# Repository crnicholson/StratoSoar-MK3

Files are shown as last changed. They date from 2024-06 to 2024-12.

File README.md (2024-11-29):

# StratoSoar MK3 - UAVs For the Masses

<!-- **TL;DR**: The StratoSoar project is a low-cost, lightweight UAV designed to be dropped from a weather balloon  at any altitude, aiming for autonomous, efficient flight to selected GPS coordinates. The hope is to get a UAV platform in the hands of educators, researchers, and hobbyists alike since StratoSoar is much smaller, lighter, and cheaper than conventional UAVs.  -->

**TL:DR**: The StratoSoar project is a low-cost, lightweight Unmanned Aerial Vehicle (UAV) designed for deployment from a weather balloon at various altitudes, aiming for autonomous and efficient flight to designated GPS coordinates. By offering a more affordable, compact, and lightweight alternative to conventional UAVs, StratoSoar aims to empower educators, researchers, and hobbyists with an accessible platform for exploration and experimentation. 

## Watch The Video

<!-- **WORK IN PROGRESS** - This project is still in the works. I don't recommend using it yet because it has the potential of being dangerous.

**NEW** - Writing code and making the PCB. 

**STATE as of 7/1/24** - Just starting development! -->

<!-- <div style="max-width: 500px; margin: 0 auto;">
  <div style="position: relative; padding-bottom: 56.25%; height: 0; overflow: hidden; max-width: 100%; height: auto;">
    <iframe style="position: absolute; top: 0; left: 0; width: 100%; height: 100%;" src="https://www.youtube.com/embed/TiqkcGWG4g8" title="StratoSoar MK2/3: A Review" frameborder="0" allow="accelerometer; autoplay; clipboard-write; encrypted-media; gyroscope; picture-in-picture; web-share" referrerpolicy="strict-origin-when-cross-origin" allowfullscreen></iframe>
  </div>
</div>

<br /> -->

YouTube Video (https://www.youtube.com/watch?v=TiqkcGWG4g8&t=1s)

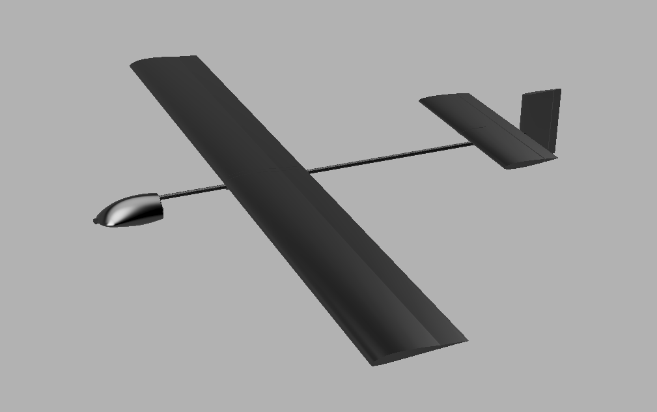
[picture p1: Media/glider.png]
Glider
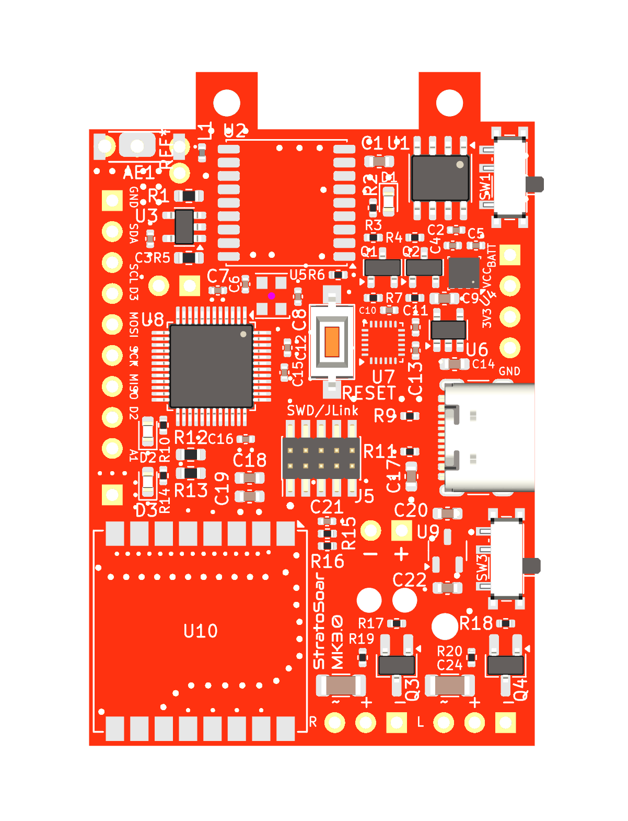
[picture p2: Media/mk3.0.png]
PCB
 | 
-- | --
<i>StratoSoar glider.</i> | <i>StratoSoar MK3.0 circuit board.</i>
Glider | PCB
<i>Computational fluid dynamic sims.</i> | <i>Soldering of the board.</i>

## What Is the StratoSoar Project?

StratoSoar is a low-power, adaptive UAV that is dropped from a weather balloon at approximately 5,000 feet, with plans to reach even higher altitudes soon. The main goal of StratoSoar is to fly to selected GPS coordinates efficiently or choose a closer, more realistic landing site without human interaction. The current aim for StratoSoar is to operate on a single 600 mAh 15 gram LiPo battery for a 10+ hour flight. 

## Now, What Is a UAV?

UAVs, or Unmanned Aerial Vehicles, are autonomous aircraft, usually in the form of planes or drones. They have many applications, such as [delivering medicine, food, and supplies](https://www.flyzipline.com/) to remote areas, participating in aerial combat with the military, and conducting aerial imaging.

### Common Types of UAVs Include:

- Quadcopter (typical drones)
- Fixed-wing aircraft (like StratoSoar)

## StratoSoar vs. Conventional UAVs

### Traditional UAVs Are Typically:

- Large (5-15 meter wingspan)
- Heavy (2-20 kg)
- Expensive ($10,000-10,000,000 USD)
- Closed source and proprietary

### StratoSoar Aims to Overcome These Limitations With:

- Weight: less than 250 grams
- Wingspan: 80 cm
- Cost: less than $150 USD
- Open source and accessible

## What Are the Uses of StratoSoar?

I'm currently considering two main concepts: an educational kit for students and hobbyists or a platform designed to study the aerodynamics of the stratosphere, a field with limited existing resources. Additionally, I'm exploring other ideas such as reusable radiosondes, systems for remote delivery of medicine and parcels, and advanced atmospheric monitoring solutions.

<!-- ## What Includes the StratoSoar Project? What Are the Different Parts of it?

StratoSoar has many different parts, and they all combine to make this project. 

- **Code** - All of the code directory, and the programs needed to run it. These include the main `.ino`s and the accompanying `.cpp` and `.h` files, along with the test files for the IMU and GPS.
- **PCB** - The circuit board is the basis of this project, it interfaces the code with the glider. StratoSoar includes the circuit board files and the schematics and everything needed to build a PCB.
- **3D Files** - StratoSoar requires some 3D printed parts to function, but these files also serve as an interactive build guide. StratoSoar includes the 3D files needed to print parts for the glider and the 3D files to assemble the glider.
- **Media** - The images and such of StratoSoar. 
- **Cutdown Mechanism** - This is the thing that helps you release the glider from the balloon payload - or whatever you want to drop it from. This includes all of the above things but will be in a separate GitHub repository.  -->

## How Does StratoSoar Work at a High Level?

<!-- StratoSoar is attached to a weather balloon via the cutdown mechanism. Once the balloon reaches the desired altitude, the cutdown mechanism drops the glider. The glider then descends, steering its way to specified coordinates. 

StratoSoar takes pride in being highly configurable and hackable, so there are many ways you change how it comes down built into the code. 

StratoSoar uses data from an IMU that goes through a Kalman filter to receive accurate AHRS, or Attitude Heading Reference System. This can tell StratoSoar the pitch, yaw, and roll of the glider. Then, StratoSoar integrates a GPS module to get the GPS coordinates. Both the GPS and the AHRS are used to compute the azimuth to find the turning angle of the glider. The turning angle tells the glider how much it needs to turn to be facing the correct yaw that will get the glider to the target location. Additionally, an algorithm is used to get the distance between the glider location's and the target location. 

With the turning angle computed, a PID mechanism is used to control the servo attached to the rudder of the glider. This PID mechanism learn from it's mistakes and can accurately aim the glider in the correct direction. 

Additionally, the glider beacons it's location at a configurable interval with LoRa for tracking. It also allows for a camera module to be added on to take photos and video. 

The glider will fly to the selected coordinates, and depending on the user configuration, will either spiral down or release a parachute above the coordinates once it has reached them to safely descend. Additionally, if the glider is too low in altitude, prior to the flight the user can enter closer coordinates as backup landing locations.  -->

StratoSoar MK3 is an advanced autonomous glider designed to operate at high altitudes, such as those reached by weather balloons. The glider is attached to a weather balloon via a cutdown mechanism. Once the balloon reaches the desired altitude, the cutdown mechanism releases the glider, initiating its descent. The glider then navigates autonomously to specified coordinates, using a combination of sensors, advanced algorithms, and low-power electronics.

### Core Components and Functionality:

- **Autopilot System**:
    - **GPS and IMU Integration**: StratoSoar uses a custom GPS module and an IMU, both designed for low-power operation. The IMU data is processed through a Kalman filter to provide accurate Attitude Heading Reference System (AHRS) data, including pitch, yaw, and roll. This information, combined with GPS coordinates, enables precise navigation.
    - **Advanced Waypoint Navigation**: The waypoint navigation system is designed for complex flight paths, incorporating advanced turning algorithms to ensure smooth and accurate direction changes.
    - **Servo Control with PID**: A PID control mechanism governs the rudder’s servo, ensuring precise adjustments to the glider's course based on real-time feedback.

- **Communication and Data Logging**:
    - **LoRa Telemetry**: The glider continuously beacons its location via LoRa communication, which includes forward error correction for reliable data transmission. This allows for real-time tracking and data collection.
    - **Data Logging**: Critical flight data, including sensor readings and GPS coordinates, are logged using a combination of SD card and EEPROM storage, optimized for low power consumption.
    - **Camera**: If configured, the glider uses a custom designed camera module to take photos at specific coordinates or record the entire flight.  

- **Modularity and Customization**:
    - **Hackability**: StratoSoar is designed to be highly configurable and hackable. Users can customize its descent strategy, whether by spiral descent, parachute deployment, or alternative landing locations. The codebase is modular, allowing for easy modifications or the addition of new features.
    - **Camera Module**: An optional low-power camera module can be added to capture photos or video during the flight, with Python scripts available for post-processing the footage.

- **Ground Station and Data Handling**:
    - **Ground Station**: The ground station, built on an ESP32 platform, receives telemetry data from the glider via LoRa. It logs this data locally and communicates with a server using HTTP requests. A Flask-based uploader script then transfers the data to SondeHub for analysis and storage.

- **PCB Design**:
    - **StratoSoar MK3 PCB**: The main PCB, optimized for power efficiency, size, and cost, integrates over 100 components, managing the various systems onboard.
    - **Additional PCBs**: Supporting PCBs, such as those for the GPS module, LoRa communication, camera, and IMU, are designed for specific tasks, enhancing the glider's overall functionality.

### Operation and Recovery:

Upon release from the weather balloon, StratoSoar begins its guided descent following waypoints or single target coordinate. It calculates the optimal flight path using its GPS and AHRS data, making real-time adjustments to its trajectory through the PID-controlled servo system. Depending on user configurations, the glider can either glide smoothly to the target coordinates, initiate a spiral descent, or deploy a parachute for a safe landing.

If the glider's altitude drops below a certain threshold, backup landing coordinates can be used to ensure a safe recovery. Throughout the flight, the glider’s location is continuously transmitted, allowing for easy tracking and recovery.

## File System and More Project Info

I'm only listing the key items, leaving out all the unnecessary stuff. This should give you a general sense of the project and all its features. Note that this is also only stuff I did during Hack Club Arcade.

- `Code/autopilot`: (5000 lines of code!)
    - `autopilot.ino`: The script that ties all of these files together.
    - `gps.cpp`: GPS code custom-made for low-power.
    - `waypoint.cpp`: Custom waypoint flight with advanced turning.
    - `lora.cpp`: LoRa communications with complex forward error correction.
    - `sd.cpp` + `eeprom.cpp`: Data logging in a low-power manner.
    - `servo.cpp`: Ultra low-power servo functions.
    - `bme280.cpp`: Weather data sensor.
    - `imu.cpp`: An interial measurement unit running a Kalman filter.
- `Code/groundStation`: 
    - `groundStation.ino`: The code for the receiving station of the LoRa telemetry, uses ESP32 and HTTP requests to communicate with the server, also locally logs data. 
    - `uploader/flaskUploader.py`: A Flask server that uses an API to put all the data on SondeHub. 
- `Code/camera`: Utilization of a low-power camera module and Python scripts for conversion.
- `Code/calculator`: Python script to parametrically create flying wing glider. 
- `PCB/StratoSoar-MK3.0`: The main PCB consisting of over 100 components, optimized for power, size, and cost.
- `PCB/gpsBreakout`: A PCB designed for testing a cheap, $2 Chinese GPS module.
- `PCB/loRa`: The ground station to receive the glider's data. 
- `PCB/camera`: A breakout board for a low-power camera module. 
- `PCB/imuBreakout`: One of the first breakout boards made for a new Interial Measurement Unit. 
- `3D Files/cardboardGlider`: Parametric Fusion 360 design for a folding origami glider. 
- `3D Files/StratoSoar Rev2 v36`: High efficiency glider.

## A Quick Note on MK1, MK2, Naming, and Revisions

StratoSoar MK1 was the precursor and the spark to StratoSoar MK2. StratoSoar MK1 was officially developed from October 1st to July 30th, although StratoSoar MK2 was unofficially being worked on in the months of March through June. StratoSoar MK1 failed to fly autonomously, and it also failed to release from the balloon. Major upgrades have been made since then.

StratoSoar MK2 officially started on October 1st, and will end has now ended. It was a success. 

StratoSoar MK3 officially started on June 1st, and will end in quite some time when I launch it from a weather balloon. A new major revision (eg. MK4) will come out every time when I release the glider from the balloon in the Summer. After the Summer, work on the next revision begins, with many updates and new features. 

<!-- A new sub-revision (for lack of better word) comes out every time I make a new PCB. For example, my first version of my PCB was MK2.0. At the time of writing, the current version of StratoSoar is MK2.1. A new version of 3D model is denoted by the Rev number. Rev starts at 0. 0 and 1 are not shown in this repo because they didn't turn out very good. The physical gliders are denoted by the 3D model number. Sometimes a small change is made with glider so the name of the glider is Rev x.x, for example. Sometimes the same happens with the 3D model, again it would be x.x. To put this in practice, the final glider may be MK2.5 Rev 7.3.1. The code has no version history in the way the 3D models and the PCB do. -->

Also, I use "we" a lot in this writing. This usually refers to myself or this project, but it also refers to my small team over at New England Weather Balloon Society.

One last thing. When I refer to StratoSoar, I am referring to the project as a whole, but more specifically, the most recent version. 

<!-- ## Watch my Talk About StratoSoar MK2 The North East HamXpo! -->

## Is This Legal?
Yes! During flight, the ground operator has no ***direct*** control over the flight path, i.e. via a radio. Because of this, and it being unpowered, it qualifies as a free flight glider. Free flight gliders have very little regulations. You can think of them as a paper airplane. 

## Can I Buy a Kit or a Complete Product?

Currently, StratoSoar is not available to purchase online as a kit or complete product. We have plans in the next few years to release a kit for schools, education centers, hobbyists and a complete product for industry at an affordable price. You are welcome to make one in the mean time!

## How Can I Make One? Are There Docs?

One of the goals of StratoSoar was to make an affordable and open source system for anyone to perform stratospheric research, so all the files are available for free. This means that you can construct StratoSoar from scratch. **A guide to do this will be available soon.**

<!-- It is still in the works, but you can check out `DOCS.md` under the `Docs` folder.**  -->

## Helpful Sources and Credits

I'm in the midst of compiling this.

## Cutdown Mechanism

[See my other WIP GitHub repo.](https://github.com/crnicholson/Cutdown-Mechanism)

## Funding and Support

We currently have <u>**very**</u> limited funding to complete this project. We would **love any donations or sponsorships** we could get to elevate (no pun intended) this project to the next level. If you don't want to donate, but want to help out, we would love your support with other areas of this project. Reach out to me if you have interest at:

- [newbsballoons@gmail.com](mailto:newbsballoons@gmail.com) (organization email, recommended).

- [charlienicholsonr@gmail.com](mailto:charlienicholsonr@gmail.com) (personal email).

## Special Thanks

This project would not be possible without the following individuals:

- Max Kendall (W0MXX) for working closely together with me.

- Mike Malis for helping with the design of the glider. 

- Brett Miwa for schematic review, PCB design, electrical theory, and boost converter circuitry design.

- Bob Phinney (K5TEC) for providing NEST and securing funding.

- Mark Jessop (VK5QI) for answering all of my questions.

- Mike Hojnowski (KD2EAT) for PCB design and hardware/software debugging.

- Paul Hamilton for helping me with FAA regulations.

- My parents!

And these entities:

- Hack Club, for providing support for projects like this. 

- New England Sci-Tech (NEST) for providing a maker space to work, funding, and hosting NEWBS.

- New England Weather Balloon Society (NEWBS) for expertise and the opportunity.

- Bagel Fund, for providing funding. 

## Affiliate Programs and Projects

- **Hack Club** - Hack Club is a non-profit designed for teenagers that provides support for projects like this. 
- **NEWBS** - Max and Seth Kendall of NEWBS, or New England Weather Balloon Society, are helping me launch my project from a balloon. They are dedicated to helping people in New England launch weather balloons. 
- **New England Sci-Tech** - Bob Phinney of NEST is hosting NEWBS. NEST is a great maker space. If you are in the Greater Boston Area, go check them out!
- **StratoScience** - This is the official class that I'm in helping me launch my project. This is a high altitude engineering class for teens. Check them out if your are in the Greater Boston area!

## Still Have Questions?

Do you have any questions? Are the docs incomplete and you want to ask anything? Do you just want to say hi (or how cool my project is!)?

Reach out to me at [charlienicholsonr@gmail.com](mailto:charlienicholsonr@gmail.com).

## Flights

# Mid August

The glider was realeased from 5,000 feet. You can see the launch video [here](https://www.youtube.com/watch?v=DZU_8TDUlJg). You can find data on the release [here](https://www.youtube.com/watch?v=TiqkcGWG4g8).

## License

Both the software and documentation are under the [GNU GPL v3 license](https://choosealicense.com/licenses/gpl-3.0/). The hardware and the 3D files are under the [CERN Open Hardware Licence Version 2 - Strongly Reciprocal](https://choosealicense.com/licenses/cern-ohl-s-2.0/). The media is under the [CC BY 4.0 DEED](https://creativecommons.org/licenses/by/4.0/).

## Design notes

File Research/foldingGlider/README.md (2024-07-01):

# This is for Hack Club Arcade

This is a glider that is very easy to manufacture. You simply cut it out with a laser, plotter, CNC, or another tool and fold it up. It is designed to be outfitted with my custom electronics and to be used in disaster releif. My goal is for the entire bundle to be less than $75 to make it open to everyone. 

# Gallery

All images should be in the sessions on Hack Club Slack.

# Research Sessions

### [Session](https://hackclub.slack.com/archives/C06SBHMQU8G/p1719795937090849)

During this session, I delved into researching flying wing design. I started by watching videos and reading documents, focusing on aspect ratios and design parameters like taper, sweep, wingspan, chord, area, and wing cube loading (WCL). I decided on an aspect ratio of 6 for my model and aimed for a WCL of 7. I encountered some challenges with a Python script I was developing but managed to fix it to calculate surface area correctly based on weight and WCL. By the end of the session, I was working on calculating the wing sweep angle.

### [Session](https://hackclub.slack.com/archives/C06SBHMQU8G/p1719789537091729)

Swept wings decrease drag but also reduce lift and are beneficial near supersonic speeds. They act like a lever, helping balance the center of gravity (CG) and provide better leverage for the plane’s elevons.

However, swept wings can cause yaw and roll cycles due to uneven lift, leading to instability. Wing fences and tip fins improve stability by mitigating turbulence and must be positioned behind the CG to maintain positive stability. Tip fins also enhance yaw stability by preventing air from below the plane from causing additional drag.

The videos explain the concepts of center of gravity (CG) and center of pressure (CP). CG is fixed, but CP changes with the angle of attack, which can cause instability. On conventional aircraft, tails provide a downward force to balance CG and CP. It’s crucial to place the CG far in front of the CP for stability, similar to a dart’s design.

Reflex, the upturned trailing edge, acts like a tail for stability but decreases efficiency. Symmetrical airfoils are used for better stability and to reduce the need for reflex.

### [Session](https://hackclub.slack.com/archives/C06SBHMQU8G/p1719598218516089)

So to summarize my last session, you can cut foam board with a 5 watt laser diode only if the foam board is black because of the wavelengths interfering. Black foam board is about 4.50 per sheet, so not too expensive. I may go this route.

I watched this video: https://www.youtube.com/watch?v=T5YABSqPOY0. It was very helpful for me to understand cutting cardbaord on a laser diode. It seems to work much better than a high power CO2 laser, like a Glowforge. It does take some time, though. The person had the speed at 30 mm/s and 40 PASSES, which is a lot of passes. If I get a laser, I may experiment with fewer passes and decreased speed to do it quicker. This seems like the best solution for manufacturing cardboard sheets, seeing as diode lasers are much larger than CO2 lasers for much cheaper. I might buy one, we’ll see.

So I took a break to research laser cutter safety. They aren’t very safe and there’s no way my parents are letting me get one even if I pay for it. This is sad because they are perfect for my needs. However, my maker space has one but the working space of it is very limiting. Because of this I will research alternate routes.

More research to report! There aren’t any machines that can cut cardboard as well as a laser. However, a Cricut can cut cardboard quite well. The only problem with the Cricut is that they have a maximum width of 12 inches. That isn’t enough. I shall continue researching until I find a way to cut this cardboard. I may look into that needle cutter again because of how cheap and easy to use it is. It is also safe to use which is nice. (edited) 

I watched this video, it wasn’t very helpful: https://www.youtube.com/watch?v=N42lrWzGQjw. I also watched this video: https://www.youtube.com/watch?v=kho1yvjRKxQ, and it shows how CNCs can cut cardboard quite well. Unfortunately, CNCs are big and expensive and I don’t have one and neither does my maker space. I guess I need to build one! (edited) 

Did more research and I found out that I cannot cut foam core with my hot wire CNC cutter. I think the only option left now is to adapt my CNC foam cutter to use a needle cutter or a drag cutter. I will research both.

So, yes it is possible to make a CNC drag cutter. This seems really cool. The thing I’m wary about though is if my CNC foam cutter can hold all the heavy stuff to control the drag cutter.

### [Session](https://hackclub.slack.com/archives/C06SBHMQU8G/p1719593377357869)

I plan to research laser cutters, specifically for cutting foam and cardboard. Initially, it seems that a diode laser might be suitable for cutting foam board, but there are other considerations. For instance, some people suggest using a CO2 laser, which is much more expensive, around $3,000, compared to diode lasers, which cost around $200.

According to Reddit, the type of foam board matters significantly. They recommend using foam board with a cardboard backing, known as art board. Additionally, it's crucial to have an air assist feature to blow away flames that may arise during cutting, as some foam materials are prone to catching fire. Good ventilation or wearing a respirator is also essential for safety.

White foam doesn't work well with lasers because it reflects all colors. For such materials, a special foam cutter or a CO2 laser is required. I came across a discussion about a needle cutter on the LightBurn Software forum. The needle cutter operates by moving a needle up and down rapidly, penetrating the foam board to make precise cuts. However, constructing a needle cutter seems quite labor-intensive.

Given these insights, it's clear that diode lasers are not suitable for cutting certain types of foam due to their different wavelengths.

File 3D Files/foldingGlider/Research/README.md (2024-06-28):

# This is for Hack Club Arcade

This is a glider that is very easy to manufacture. You simply cut it out with a laser, plotter, CNC, or another tool and fold it up. It is designed to be outfitted with my custom electronics and to be used in disaster releif. My goal is for the entire bundle to be less than $75 to make it open to everyone. 

# Gallery

All images should be in the sessions on Hack Club Slack.

# Research Sessions

## https://hackclub.slack.com/archives/C06SBHMQU8G/p1719598218516089

So to summarize my last session, you can cut foam board with a 5 watt laser diode only if the foam board is black because of the wavelengths interfering. Black foam board is about 4.50 per sheet, so not too expensive. I may go this route.

I watched this video: https://www.youtube.com/watch?v=T5YABSqPOY0. It was very helpful for me to understand cutting cardbaord on a laser diode. It seems to work much better than a high power CO2 laser, like a Glowforge. It does take some time, though. The person had the speed at 30 mm/s and 40 PASSES, which is a lot of passes. If I get a laser, I may experiment with fewer passes and decreased speed to do it quicker. This seems like the best solution for manufacturing cardboard sheets, seeing as diode lasers are much larger than CO2 lasers for much cheaper. I might buy one, we’ll see.

So I took a break to research laser cutter safety. They aren’t very safe and there’s no way my parents are letting me get one even if I pay for it. This is sad because they are perfect for my needs. However, my maker space has one but the working space of it is very limiting. Because of this I will research alternate routes.

More research to report! There aren’t any machines that can cut cardboard as well as a laser. However, a Cricut can cut cardboard quite well. The only problem with the Cricut is that they have a maximum width of 12 inches. That isn’t enough. I shall continue researching until I find a way to cut this cardboard. I may look into that needle cutter again because of how cheap and easy to use it is. It is also safe to use which is nice. (edited) 

I watched this video, it wasn’t very helpful: https://www.youtube.com/watch?v=N42lrWzGQjw. I also watched this video: https://www.youtube.com/watch?v=kho1yvjRKxQ, and it shows how CNCs can cut cardboard quite well. Unfortunately, CNCs are big and expensive and I don’t have one and neither does my maker space. I guess I need to build one! (edited) 

Did more research and I found out that I cannot cut foam core with my hot wire CNC cutter. I think the only option left now is to adapt my CNC foam cutter to use a needle cutter or a drag cutter. I will research both.

So, yes it is possible to make a CNC drag cutter. This seems really cool. The thing I’m wary about though is if my CNC foam cutter can hold all the heavy stuff to control the drag cutter.

## https://hackclub.slack.com/archives/C06SBHMQU8G/p1719593377357869

Note: being lazy with the spelling, sorry! :)

will research lasercutters

i need to laser cut foam and cardboard

i also need to research flying wings bc I have no clue about their aerodynamics

i’ll document my findings in a readme file

seems like a diode laser is the best for cutting foam board

okay, some people are saying co2 laser

co2 lasers are like 3,00 dolla though

and diode lasers are only $200

reddit also says that the foam board matters

they say to get the foam board that has a cardboard backing - called art oard

and you need air assist to blow away the flames if they show up - some foam makes flames

they also recommend having good ventilation or wearing a respirator

oh, interesting

white foam doesn’t work very well because it reflects all color

you apparently need a special foam cutter or a co2 laser

i shall research this needle cutter

https://forum.lightburnsoftware.com/t/cutting-dollar-tree-foam-board/97158

so the needle cutter is similar to blot which is pretty rad

just a bit bigger

so it works by having a needle go up and down really really quickly

it basically penetrates the foam board and makes a fairly precise cut

it seems like it would be too much work to make though

so I’m going to research further into lasers

okay, diode lasers can’t do it! interesting! it’s mainly bc of the different wavelength

you need a co2 laser

which are super expensive.

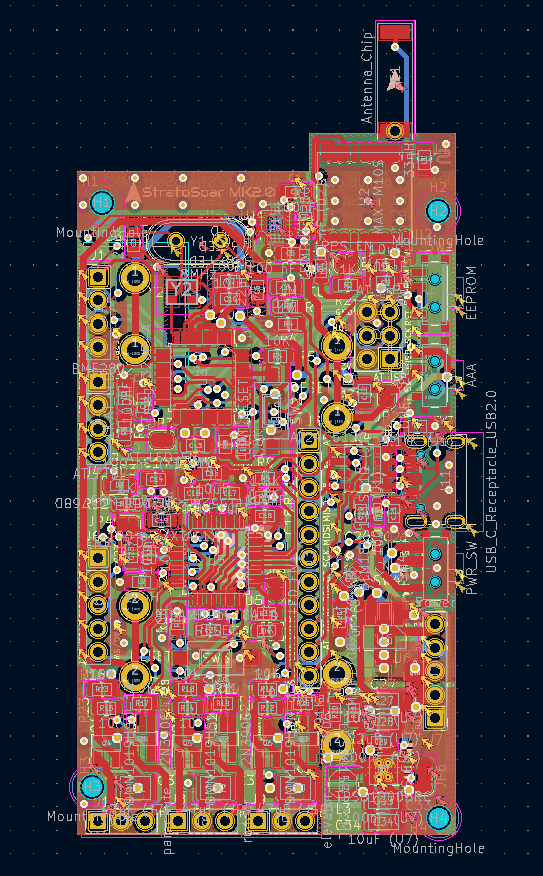
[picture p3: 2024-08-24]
Media/video/Electronics/MK2.0 board design.png

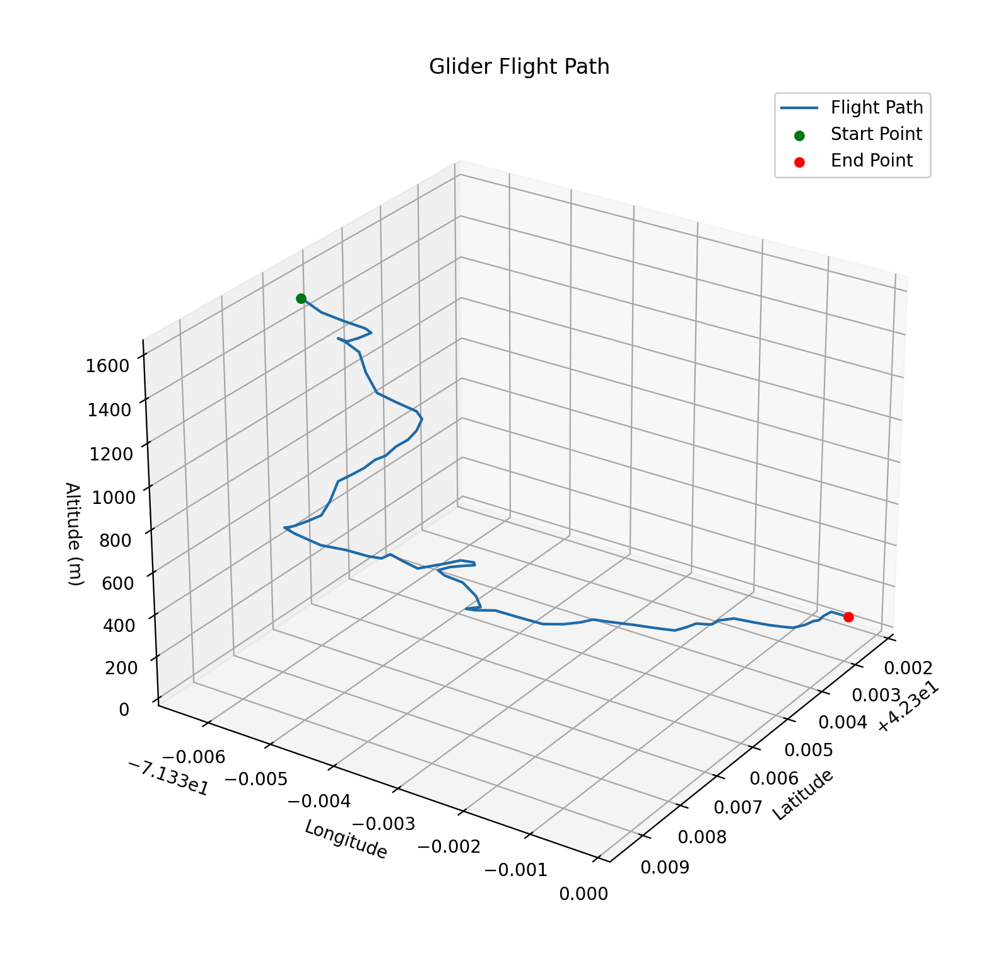
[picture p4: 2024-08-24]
Media/video/Flight path.png

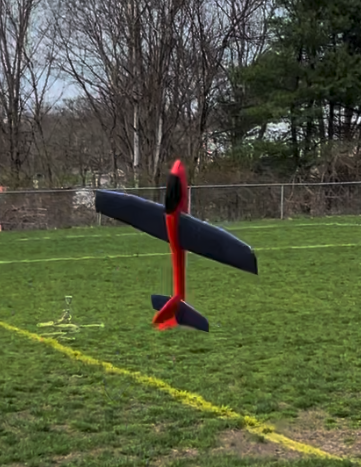
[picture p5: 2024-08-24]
Media/video/Fails/Glider flying upward.png

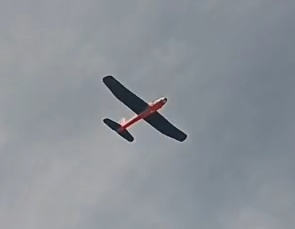
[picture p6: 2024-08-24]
Media/gliderFlying.png

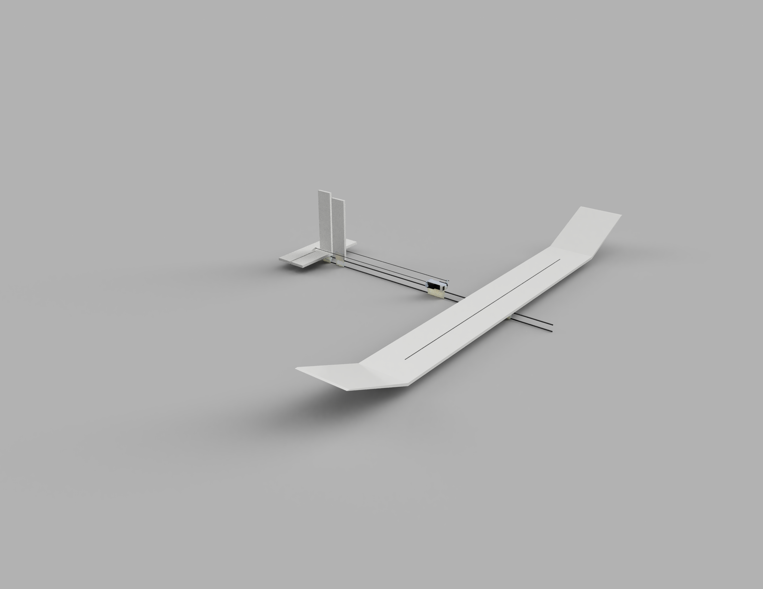
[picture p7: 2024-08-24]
Media/video/CAD/v1 render.png

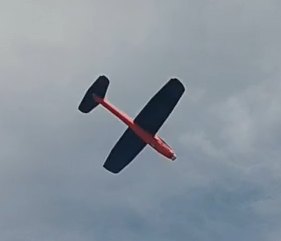
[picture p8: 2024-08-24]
Media/video/Glider action photos/Glider flying down.png

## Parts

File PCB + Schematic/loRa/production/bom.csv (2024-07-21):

Designator | Footprint | Quantity | Value | LCSC Part #
BT1 | BatteryHolder_Keystone_2462_2xAA | 1 | 3V
D1 | LED_D3.0mm | 1 | RED
J1 | PinHeader_1x08_P2.54mm_Vertical | 1 | Left
J2 | PinHeader_1x08_P2.54mm_Vertical | 1 | Right
J3 | PinHeader_1x05_P2.54mm_Vertical | 1 | GPS
J4 | PinHeader_1x10_P2.54mm_Vertical | 1 | MPU-9250
J7 | PinHeader_1x04_P2.54mm_Vertical | 1 | OLED
R1, R2 | R_Axial_DIN0207_L6.3mm_D2.5mm_P7.62mm_Horizontal | 2 | 1.8 K
R3 | R_Axial_DIN0207_L6.3mm_D2.5mm_P7.62mm_Horizontal | 1 | 1 K
SW1 | SW_Slide_SPDT | 1 | SW_SPDT
U1 | MODULE_ESP32_DEVKIT_V1 | 1 | ESP32-DEVKIT-V1

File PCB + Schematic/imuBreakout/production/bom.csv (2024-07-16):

Designator | Footprint | Quantity | Value | LCSC Part #
C1, C2, C3 | 0402 | 3 | 100 nF | C1525
C4, C5 | 0402 | 2 | 1 uF | C52923
J1 | PinHeader_1x05_P2.54mm_Vertical | 1 | Header
Q1, Q2, Q3 | SOT-23 | 3 | BSS138 | C5224268
R1, R2, R3, R4, R5, R6 | 0402 | 6 | 10 K | C25744
U1 | InvenSense_QFN-24_3x3mm_P0.4mm | 1 | ICM-20948 | C726001
U2 | SOT-23-5 | 1 | CJ6206B18M | C2829375

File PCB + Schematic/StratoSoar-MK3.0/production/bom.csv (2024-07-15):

Designator | Footprint | Quantity | Value | LCSC Part #
AE1 | ANT_1575AT_JOT-L | 1 | 1575AT43A0040001E
AE2 | PinHeader_1x01_P2.54mm_Vertical | 1 | Antenna
BT1 | MS621R | 1 | MS621R
C1, C17, C18 | 0603 | 3 | 100 nF | C14663
C10, C11, C12, C13, C16, C2, C3, C4, C7, C8 | 0402 | 10 | 100 nF | C1525
C14, C20, C22, C9 | 0603 | 4 | 1 uF | C15849
C15, C5 | 0402 | 2 | 1 uF | C52923
C19 | 0603 | 1 | 10 uF | C19702
C21 | 0402 | 1 | 1 nF | C1523
C23, C24 | 1206 | 2 | 47 uF | C139825
C6 | 0402 | 1 | 100 pF | C1546
D1, D2 | 0603 | 2 | YELLOW | C72038
D3 | 0603 | 1 | ERR_RED | C2286
H1, H2, H3, H4 | MountingHole_2.2mm_M2 | 4 | MountingHole
J1 | PinHeader_1x09_P2.54mm_Vertical | 1 | Signal
J2 | PinHeader_1x04_P2.54mm_Vertical | 1 | Power
J3 | PinHeader_1x02_P2.54mm_Vertical | 1 | Button
J4 | USB_C_Receptacle_GCT_USB4105-xx-A_16P_TopMnt_Horizontal | 1 | USB-C | C136423
J5 | PinHeader_2x05_P1.27mm_Vertical_SMD | 1 | J Link | C2881910
J7 | PinHeader_1x02_P2.54mm_Vertical | 1 | Battery
J8, J9 | PinHeader_1x03_P2.54mm_Vertical | 2 | Rudder
L1 | 0402 | 1 | 33 nH | C90178
Q1, Q2 | SOT-23 | 2 | BSS138 | C5224268
Q3, Q4 | SC-59_Handsoldering | 2 | DMN1019USN-13 | C145103
R1, R12, R13, R5 | 0603 | 4 | 1.8 K | C4177
R10, R14, R2 | 0402 | 3 | 1 K | C11702
R11, R9 | 0402 | 2 | 5.1 K | C25905
R15, R16 | 0402 | 2 | 1 M | C26083
R17, R18, R3, R4, R7, R8 | 0402 | 6 | 10 K | C25744
R19, R20 | 0402 | 2 | 10 | C25077
R6 | 0402 | 1 | 220 | C25091
SW1 | SW_SPDT_PCM12 | 1 | EEPROM | C963206
SW2 | SW_SPST_CK_RS282G05A3 | 1 | RESET | C2888954
SW3 | SW_SPDT_PCM12 | 1 | PWR_SW | C963206
U1 | SOIC-8_3.9x4.9mm_P1.27mm | 1 | AT24C512C-SSHM-T | C54668
U10 | Ai-Thinker-Ra-01-LoRa | 1 | Ra-01 | C2830750
U2 | ATGM336H | 1 | ATGM336H | C90770
U3 | SOT-23-5 | 1 | BL24C32F-RRRC | C5185883
U4 | Bosch_LGA-8_2.5x2.5mm_P0.65mm_ClockwisePinNumbering | 1 | BME280 | C92489
U5 | Oscillator_SMD_EuroQuartz_XO32-4Pin_3.2x2.5mm | 1 | DSK321STD | C383430
U6 | SOT-23-5 | 1 | CJ6206B18M | C2829375
U7 | InvenSense_QFN-24_3x3mm_P0.4mm | 1 | ICM-20948 | C726001
U8 | TQFP-48_7x7mm_P0.5mm | 1 | ATSAMD21G18A-A | C78624
U9 | SOT-23-3 | 1 | XC6206P332MR-G | C5446

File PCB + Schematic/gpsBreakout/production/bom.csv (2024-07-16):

Designator | Footprint | Quantity | Value | LCSC Part #
AE1, AE2 | GPS1003 | 2 | GPS1003 | C239243
BT1 | MS621R | 1 | MS621R
C2, C3, C5 | 0603 | 3 | 100 nF | C14663
C4 | 0402 | 1 | 470 pF | C1567
D2 | 0603 | 1 | YELLOW | C72038
J2 | PinHeader_1x11_P2.54mm_Vertical | 1 | Header
L1 | 0402 | 1 | 33 nH | C90178
L2 | 0402 | 1 | 6.8 nH | C84403
R2, R3 | 0603 | 2 | 1.8 K | C4177
R7 | 0402 | 1 | 1 K | C11702
U1 | ATGM336H | 1 | ATGM336H | C90770
U2 | SOT-23-5 | 1 | BL24C32F-RRRC | C5185883
U3 | DFN150X100X80-6N | 1 | AT2659 | C92450

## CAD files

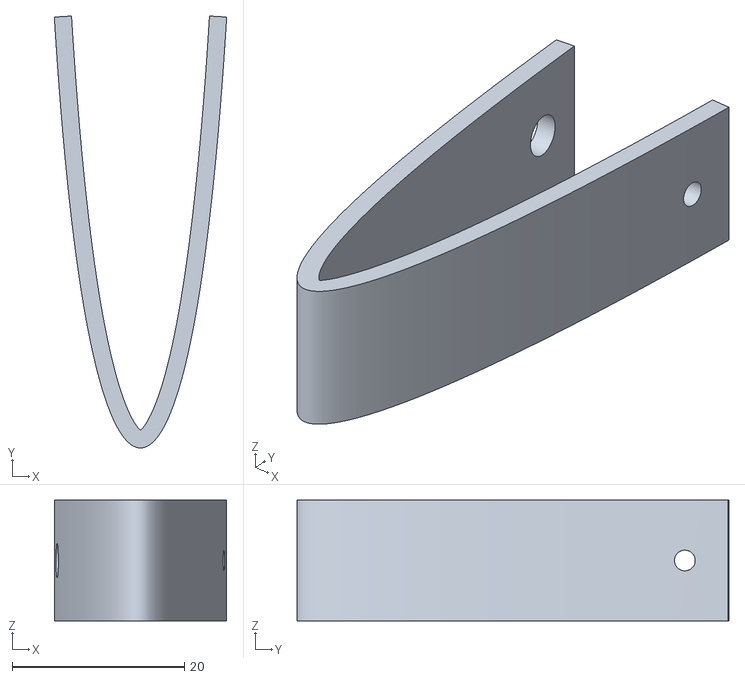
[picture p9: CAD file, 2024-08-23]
3D Files/StratoSoar Rev2 v36/StratoSoar Rev2 v36_StratoSoar Rev2 v36_Bumper_1_Body1.stl
20.0 x 50.1 x 14.0

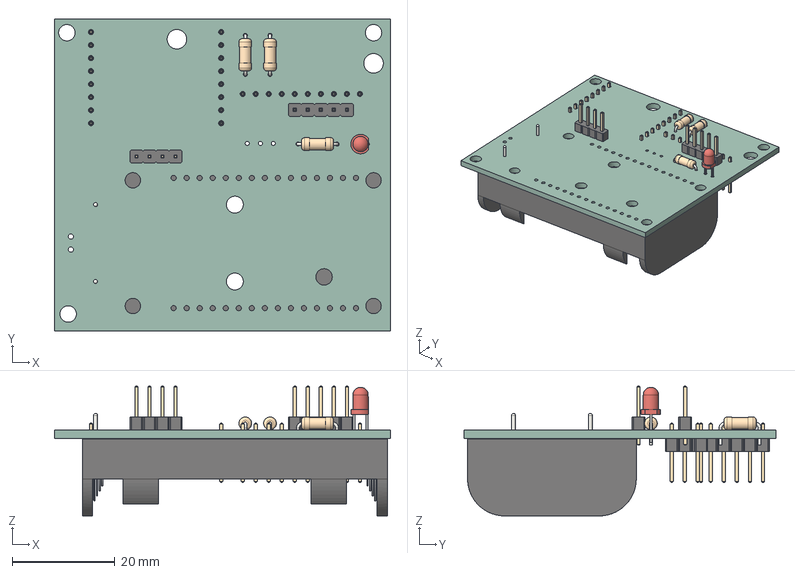
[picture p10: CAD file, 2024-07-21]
PCB + Schematic/loRa/loRa.step
65.5 x 60.8 x 25.3 mm
R_Axial_DIN0207_L63mm_D25mm_P762mm_Horizontal x 3
PinHeader_1x04_P254mm_Vertical
LED_D3.0mm
PinHeader_1x05_P254mm_Vertical
PinHeader_1x08_P254mm_Vertical x 2
Keystone_2462_2xAA
PinHeader_1x10_P254mm_Vertical
loRa_PCB

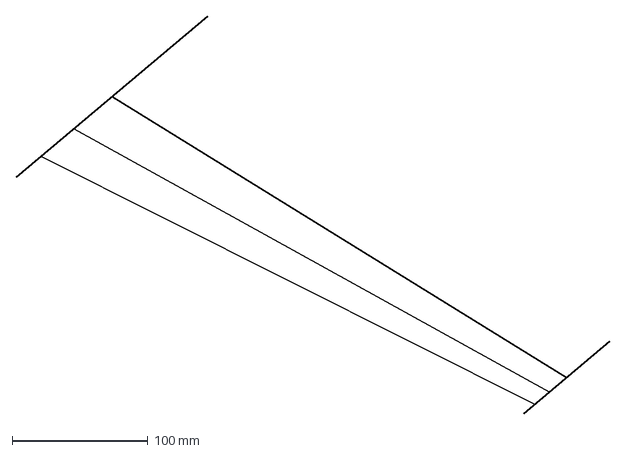
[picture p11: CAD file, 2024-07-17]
3D Files/cardboardGlider/score.dxf
438.1 x 293.4 mm

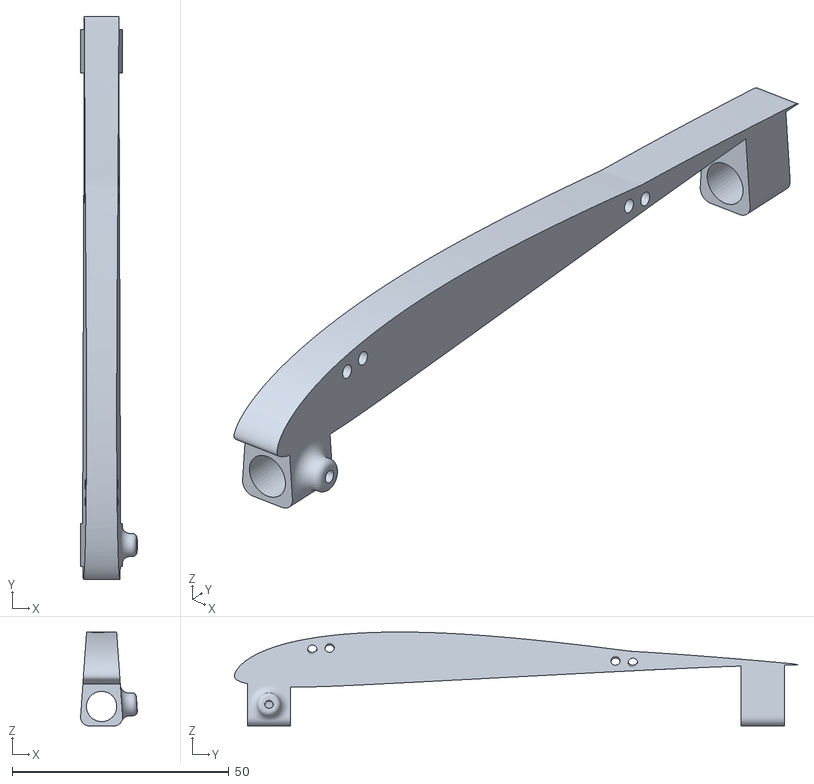
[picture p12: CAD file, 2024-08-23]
3D Files/StratoSoar Rev2 v36/StratoSoar Rev2 v36_StratoSoar Rev2 v36_Wing mount_1_Body1.stl
13.1 x 130.0 x 21.7

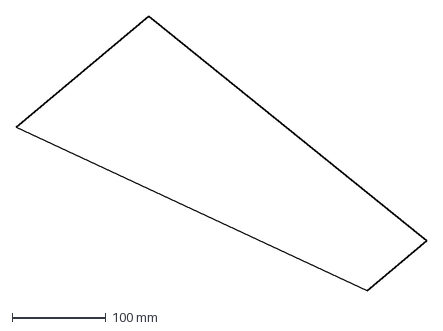
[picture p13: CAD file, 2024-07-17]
3D Files/cardboardGlider/topCut.dxf
438.1 x 293.4 mm

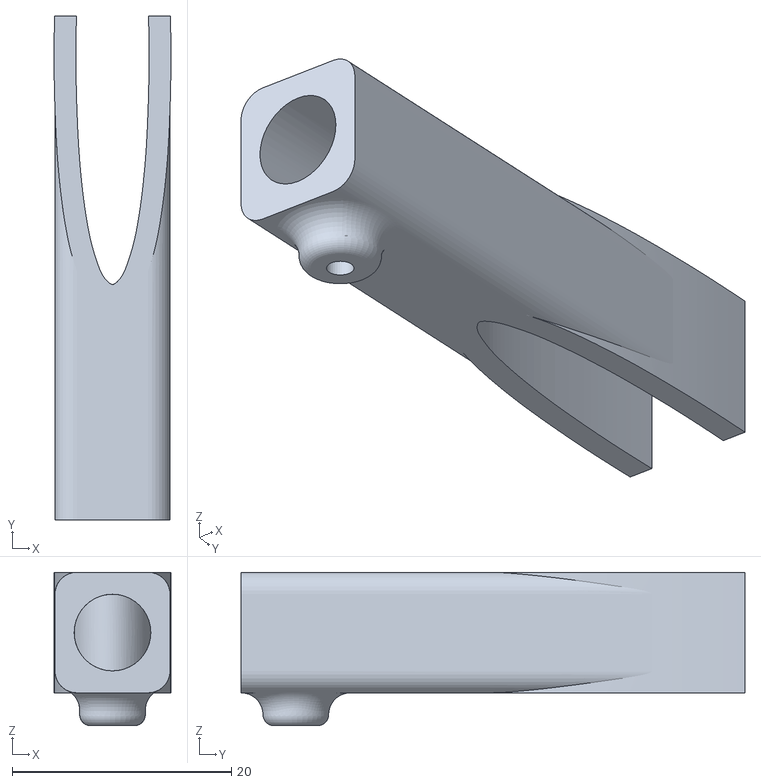
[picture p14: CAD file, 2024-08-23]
3D Files/StratoSoar Rev2 v36/StratoSoar Rev2 v36_StratoSoar Rev2 v36_Vertical mount_1_Body1.stl
10.7 x 46.0 x 14.0

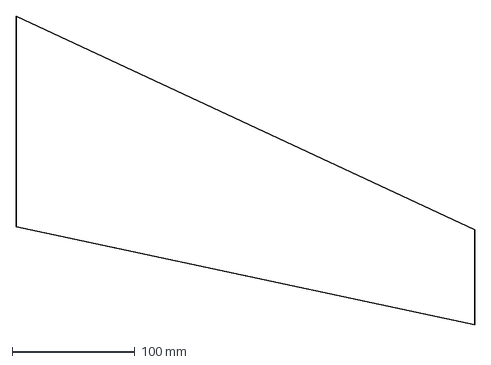
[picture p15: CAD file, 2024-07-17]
3D Files/cardboardGlider/bottomCut.dxf
374.4 x 252.1 mm

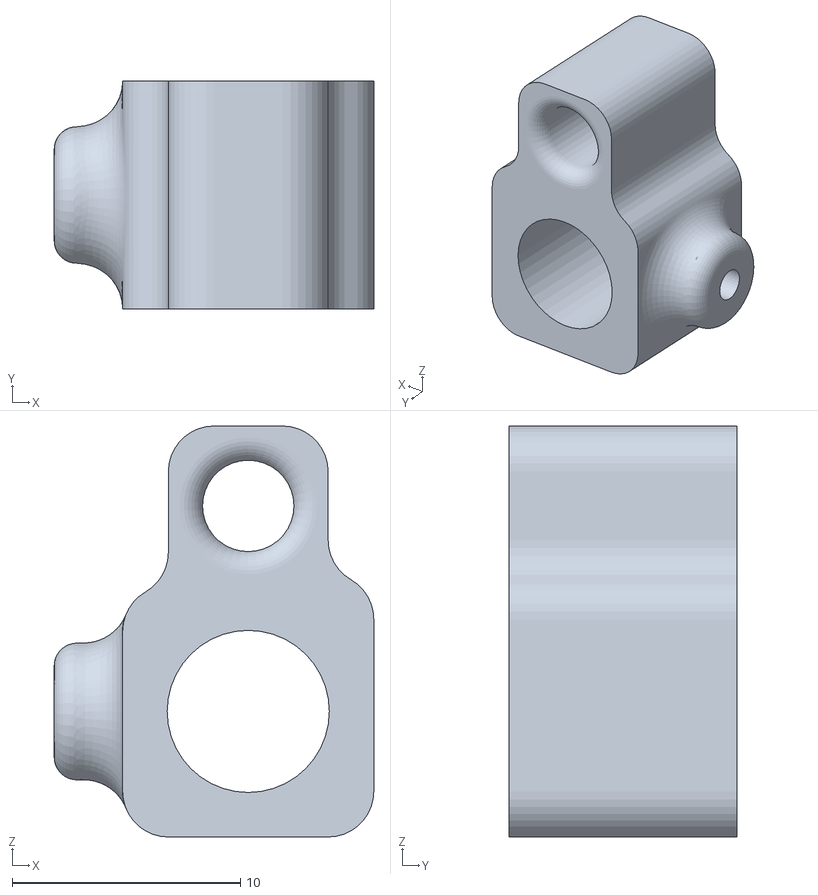
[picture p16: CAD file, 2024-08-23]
3D Files/StratoSoar Rev2 v36/StratoSoar Rev2 v36_StratoSoar Rev2 v36_Pushrod clip_1_Body1.stl
14.0 x 10.0 x 18.0

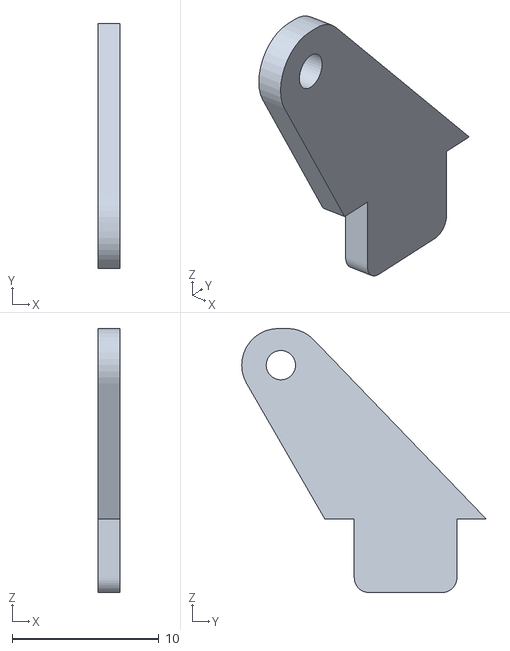
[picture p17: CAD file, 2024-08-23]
3D Files/StratoSoar Rev2 v36/StratoSoar Rev2 v36_StratoSoar Rev2 v36_Push rod horn_1_Body1.stl
1.50 x 16.7 x 18.0

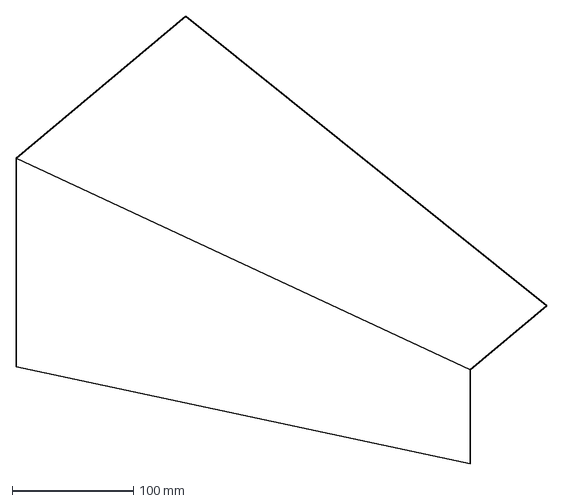
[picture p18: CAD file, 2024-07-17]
3D Files/cardboardGlider/cut.dxf
437.3 x 369.3 mm

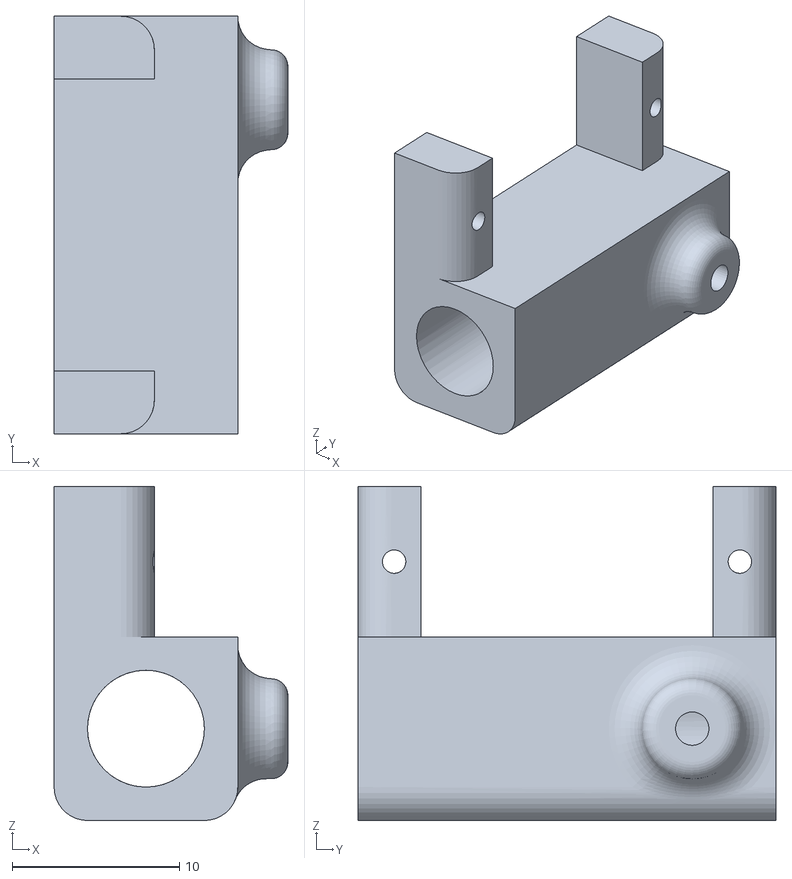
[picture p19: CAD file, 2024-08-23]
3D Files/StratoSoar Rev2 v36/StratoSoar Rev2 v36_StratoSoar Rev2 v36_Servo mount_2_Body1.stl
14.0 x 25.0 x 20.0

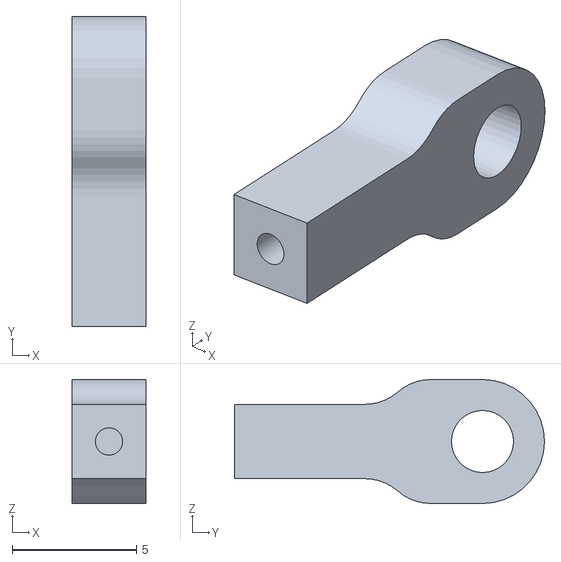
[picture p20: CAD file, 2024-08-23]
3D Files/StratoSoar Rev2 v36/StratoSoar Rev2 v36_StratoSoar Rev2 v36_Push rod connector_1_Body1.stl
3.00 x 12.5 x 5.00

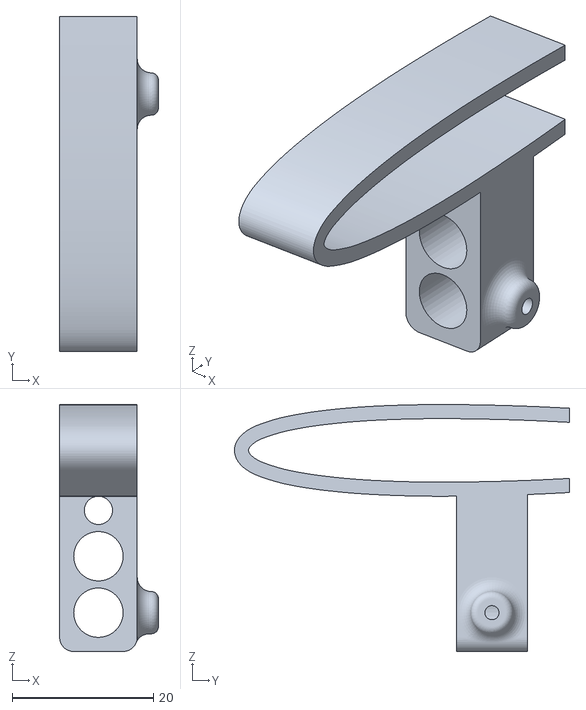
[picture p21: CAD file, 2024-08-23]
3D Files/StratoSoar Rev2 v36/StratoSoar Rev2 v36_StratoSoar Rev2 v36_Horizontal mount_1_Horizontal mount.stl
14.0 x 47.5 x 35.0

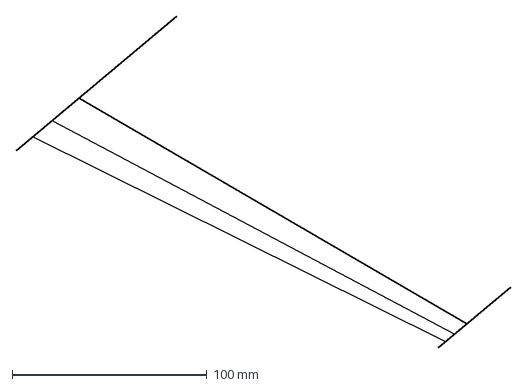
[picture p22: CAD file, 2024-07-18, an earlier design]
3D Files/cardboardGlider/deprecated/score.dxf
253.6 x 170.1 mm

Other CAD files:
3D Files/cardboardGlider/cardboardGlider v8.step
3D Files/StratoSoar Rev2 v36/StratoSoar Rev2 v36_StratoSoar Rev2 v36_Pushrod clip_2_Body1.stl
3D Files/StratoSoar Rev2 v36/StratoSoar Rev2 v36_StratoSoar Rev2 v36_Servo mount_1_Body1.stl
3D Files/cardboardGlider/deprecated/bottomCut.dxf
3D Files/cardboardGlider/cardboardGlider v5.step
3D Files/cardboardGlider/cardboardGlider v6.step
3D Files/cardboardGlider/cardboardGlider v8.f3d
3D Files/cardboardGlider/cardboardGlider v9.f3d
3D Files/cardboardGlider/deprecated/cardboardGlider v5.step
3D Files/cardboardGlider/deprecated/cardboardGlider v6.step
3D Files/cardboardGlider/deprecated/cardboardGlider v8.f3d
3D Files/cardboardGlider/deprecated/cardboardGlider v8.step
3D Files/cardboardGlider/deprecated/fin.dxf
3D Files/cardboardGlider/deprecated/topCut.dxf
3D Files/deprecated/foldingGlider/foldingGlider v1.f3d
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

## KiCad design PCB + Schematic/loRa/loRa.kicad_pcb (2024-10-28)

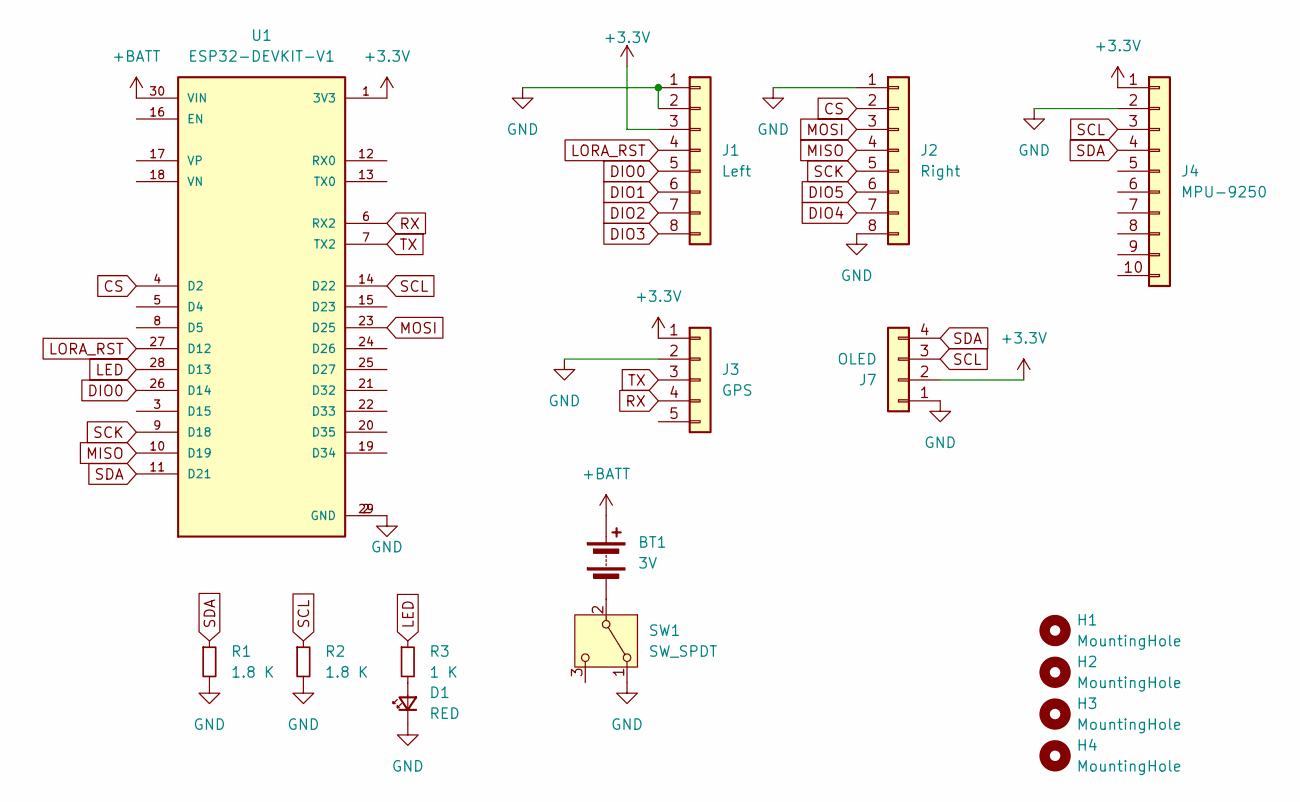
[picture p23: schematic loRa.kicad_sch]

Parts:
BT1: 3V; BatteryHolder_Keystone_2462_2xAA
D1: RED; LED_D3.0mm
H1, H2, H3, H4: MountingHole; MountingHole_3.2mm_M3
J1: Left; PinHeader_1x08_P2.54mm_Vertical
J2: Right; PinHeader_1x08_P2.54mm_Vertical
J3: GPS; PinHeader_1x05_P2.54mm_Vertical
J4: MPU-9250; PinHeader_1x10_P2.54mm_Vertical
J7: OLED; PinHeader_1x04_P2.54mm_Vertical
R1, R2: 1.8 K; R_Axial_DIN0207_L6.3mm_D2.5mm_P7.62mm_Horizontal
R3: 1 K; R_Axial_DIN0207_L6.3mm_D2.5mm_P7.62mm_Horizontal
SW1: SW_SPDT; SW_Slide_SPDT
U1: ESP32-DEVKIT-V1; MODULE_ESP32_DEVKIT_V1; PARTREV N/A

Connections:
+3.3V: J1.3, J3.1, J4.1, J7.2, U1.1 (3V3)
+BATT: BT1.1 (+), U1.30 (VIN)
CS: J2.2, U1.4 (D2)
DIO0: J1.5, U1.26 (D14)
DIO1: J1.6
DIO2: J1.7
DIO3: J1.8
DIO4: J2.7
DIO5: J2.6
GND: D1.1 (K), J1.1, J1.2, J2.1, J2.8, J3.2, J4.2, J7.1, R1.2, R2.2, SW1.1 (A), U1.2 (GND), U1.29 (GND)
LED: R3.1, U1.28 (D13)
LORA_RST: J1.4, U1.27 (D12)
MISO: J2.4, U1.10 (D19)
MOSI: J2.3, U1.23 (D25)
unnamed: BT1.2 (-), SW1.2 (B)
unnamed: D1.2 (A), R3.2
RX: J3.4, U1.6 (RX2)
SCK: J2.5, U1.9 (D18)
SCL: J4.3, J7.3, R2.1, U1.14 (D22)
SDA: J4.4, J7.4, R1.1, U1.11 (D21)
TX: J3.3, U1.7 (TX2)

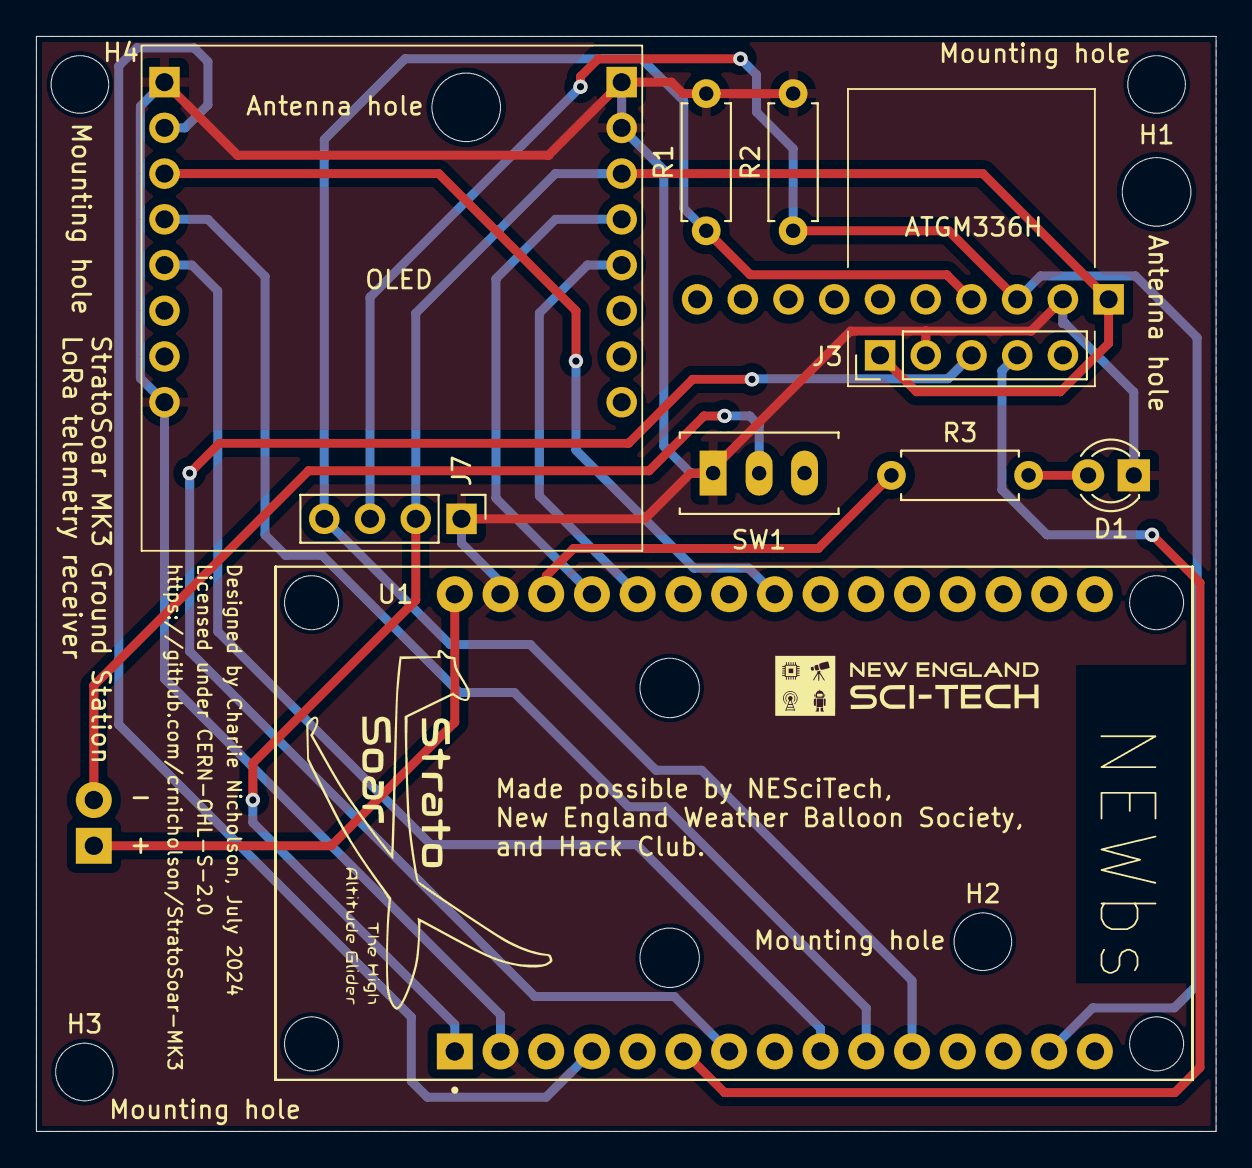
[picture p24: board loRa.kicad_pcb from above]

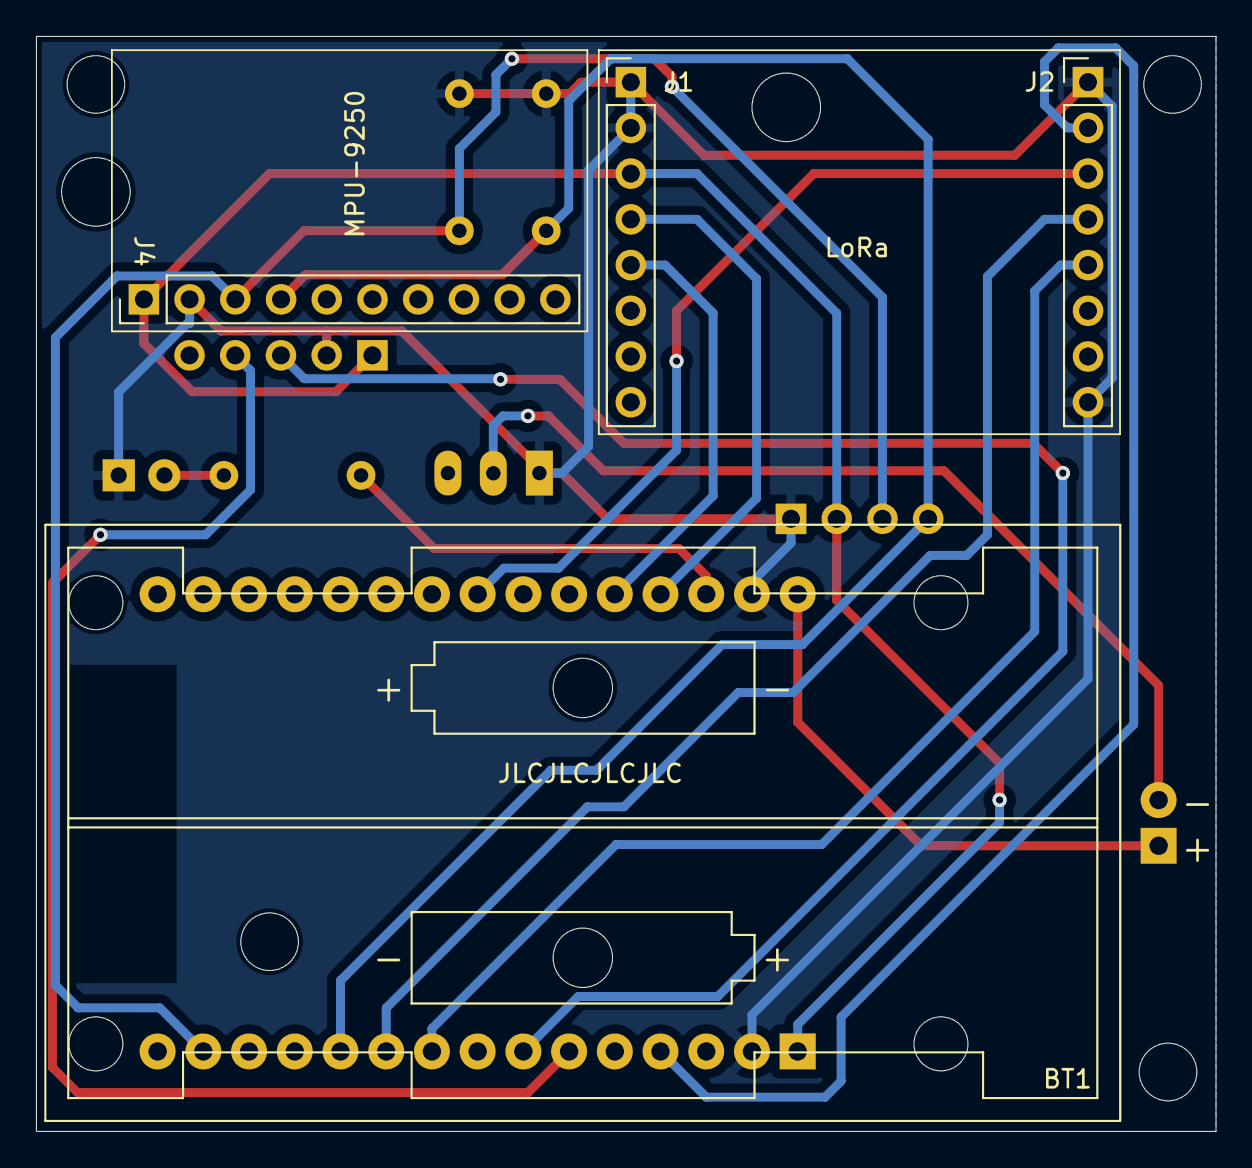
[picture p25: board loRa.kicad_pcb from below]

Board: 2 copper layers, 65.5 x 60.8 mm, 16 parts (4 on the bottom side), 16 nets.

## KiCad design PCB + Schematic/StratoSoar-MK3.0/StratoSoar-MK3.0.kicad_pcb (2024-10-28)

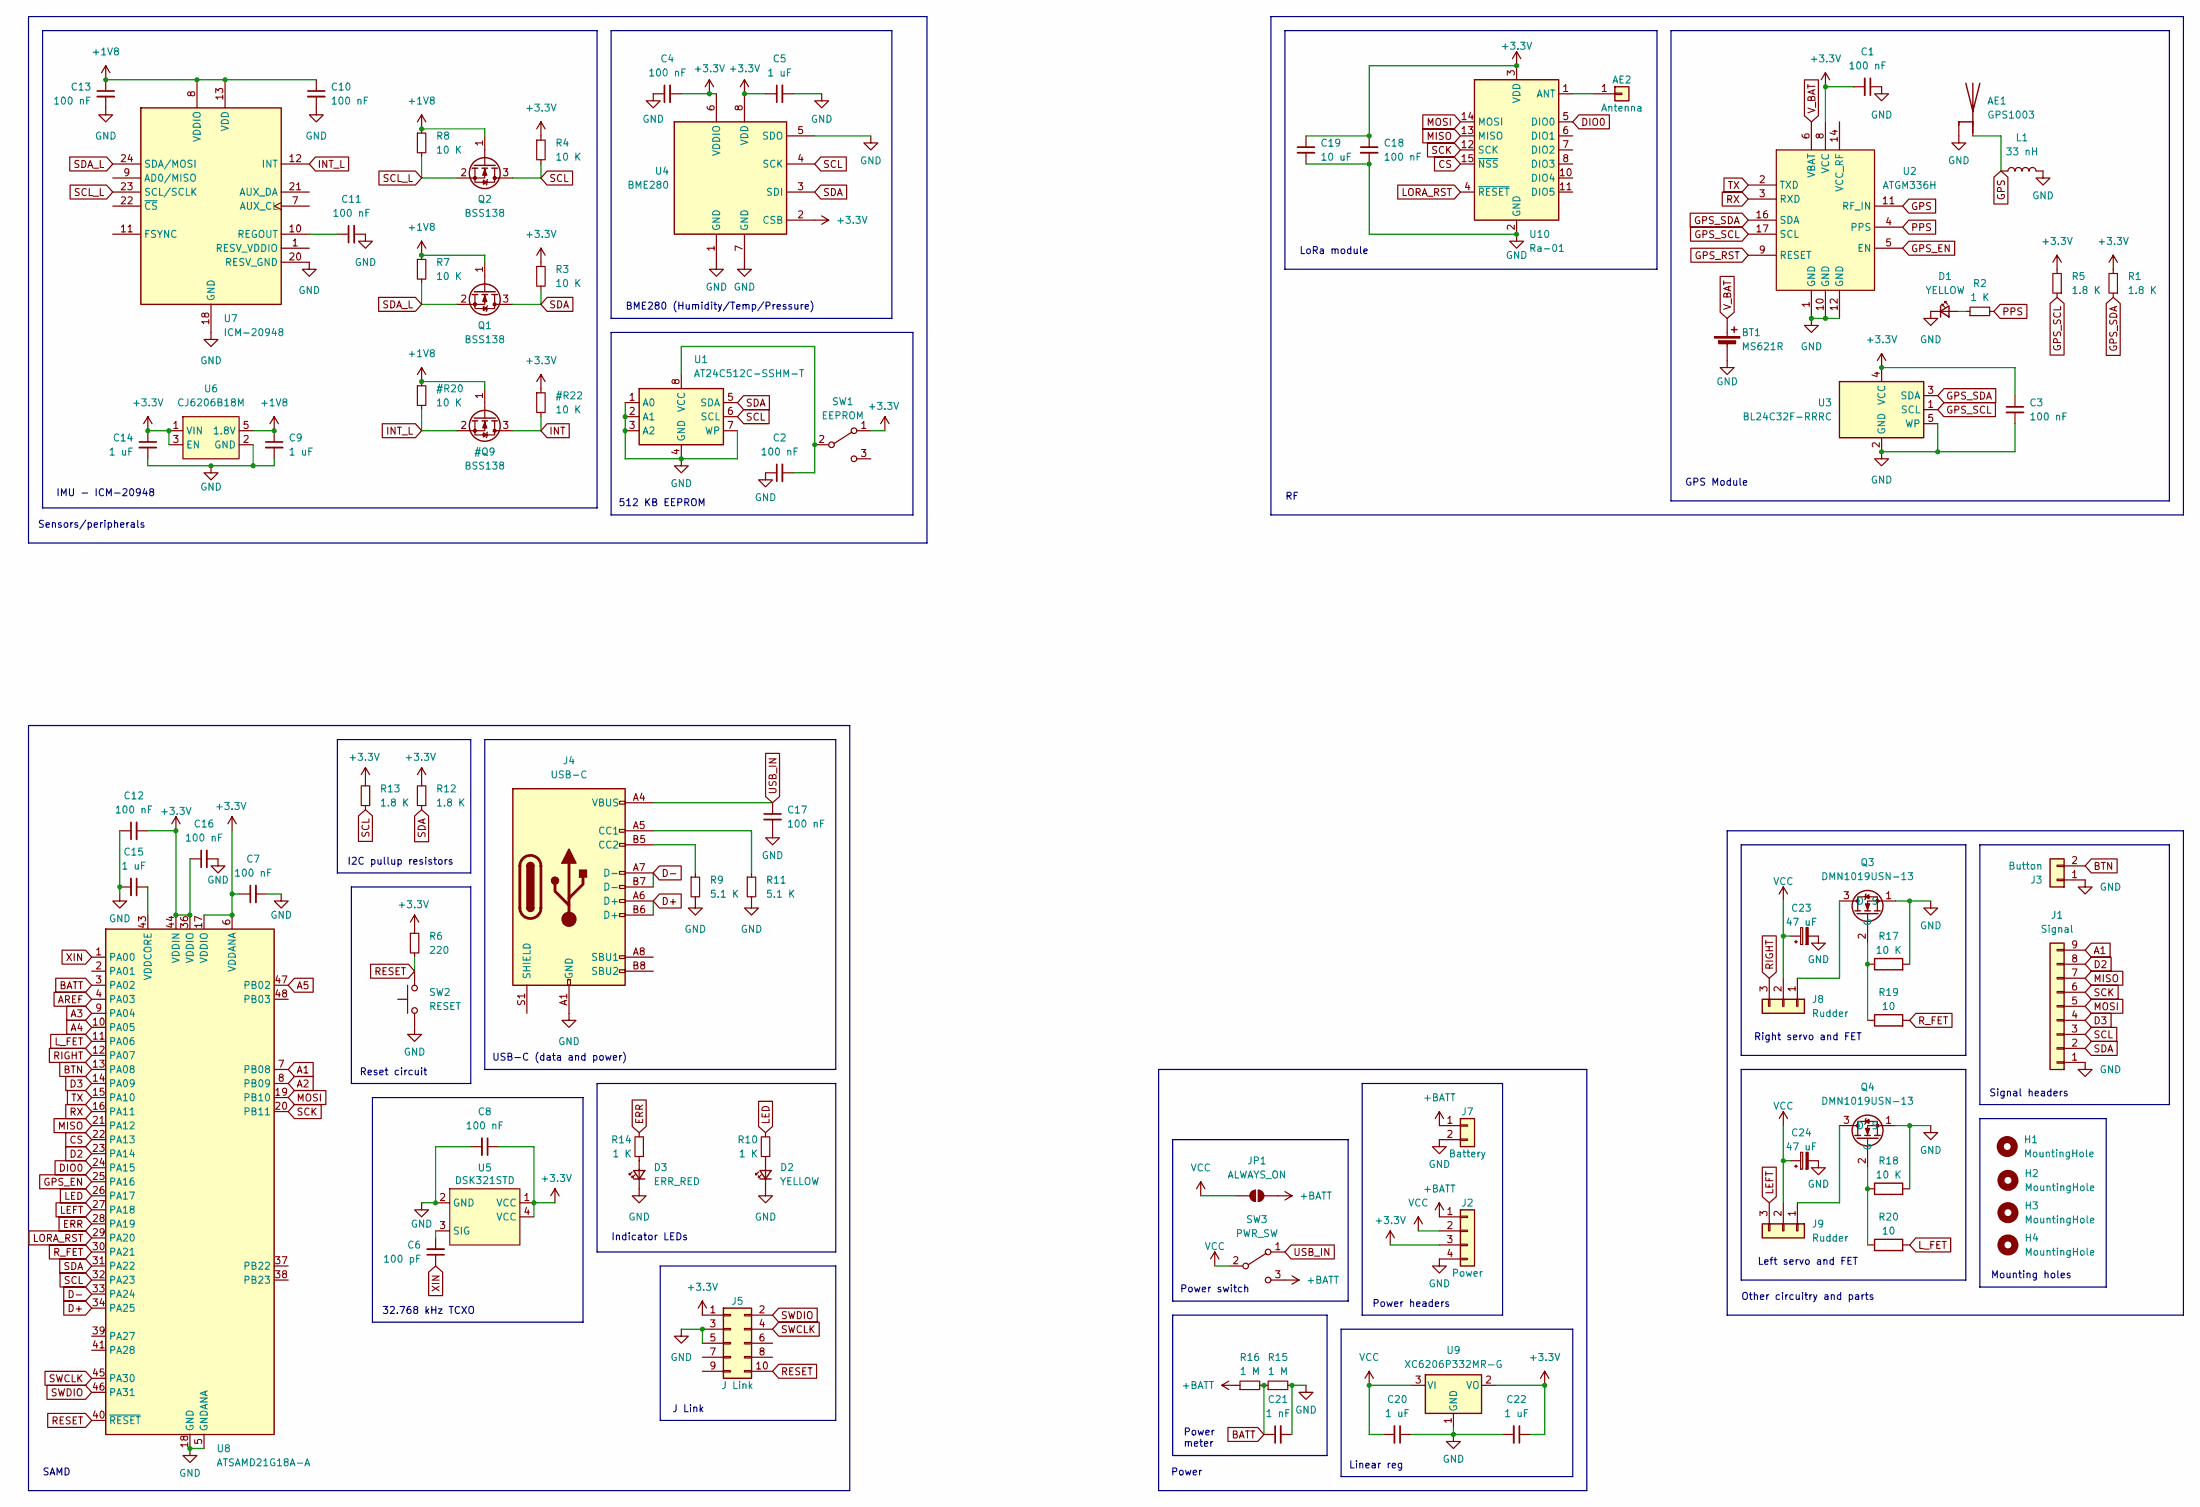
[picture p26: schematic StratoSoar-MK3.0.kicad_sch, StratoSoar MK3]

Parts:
AE1: GPS1003
AE2: Antenna; PinHeader_1x01_P2.54mm_Vertical
BT1: MS621R
C1, C17, C18: 100 nF; C_0603_1608Metric; LCSC C14663
C2, C3, C4, C7, C8, C10, C11, C12, C13, C16: 100 nF; C_0402_1005Metric; LCSC C1525
C5, C15: 1 uF; C_0402_1005Metric; LCSC C52923
C6: 100 pF; C_0402_1005Metric; LCSC C1546
C9, C14, C20, C22: 1 uF; C_0603_1608Metric; LCSC C15849
C19: 10 uF; C_0603_1608Metric; LCSC C19702
C21: 1 nF; C_0402_1005Metric; LCSC C1523
C23, C24: 47 uF; C_1206_3216Metric; LCSC C139825
D1, D2: YELLOW; LED_0603_1608Metric; LCSC C72038
D3: ERR_RED; LED_0603_1608Metric; LCSC C2286
H1, H2, H3, H4: MountingHole; MountingHole_2.2mm_M2
J1: Signal; PinHeader_1x09_P2.54mm_Vertical
J2: Power; PinHeader_1x04_P2.54mm_Vertical
J3: Button; PinHeader_1x02_P2.54mm_Vertical
J4: USB-C; USB_C_Receptacle_GCT_USB4105-xx-A_16P_TopMnt_Horizontal; LCSC C136423
J5: J Link; PinHeader_2x05_P1.27mm_Vertical_SMD; LCSC C2881910
J7: Battery; PinHeader_1x02_P2.54mm_Vertical
J8, J9: Rudder; PinHeader_1x03_P2.54mm_Vertical
JP1: ALWAYS_ON; SolderJumper-2_P1.3mm_Open_RoundedPad1.0x1.5mm
L1: 33 nH; L_0402_1005Metric; LCSC C90178
Q1, Q2: BSS138; SOT-23; LCSC C5224268
Q3, Q4: DMN1019USN-13; SC-59_Handsoldering; LCSC C145103
R1, R5, R12, R13: 1.8 K; R_0603_1608Metric; LCSC C4177
R2, R10, R14: 1 K; R_0402_1005Metric; LCSC C11702
R3, R4, R7, R8, R17, R18: 10 K; R_0402_1005Metric; LCSC C25744
R6: 220; R_0402_1005Metric; LCSC C25091
R9, R11: 5.1 K; R_0402_1005Metric; LCSC C25905
R15, R16: 1 M; R_0402_1005Metric; LCSC C26083
R19, R20: 10; R_0402_1005Metric; LCSC C25077
SW1: EEPROM; SW_SPDT_PCM12; LCSC C963206
SW2: RESET; SW_SPST_CK_RS282G05A3; LCSC C2888954
SW3: PWR_SW; SW_SPDT_PCM12; LCSC C963206
U1: AT24C512C-SSHM-T; SOIC-8_3.9x4.9mm_P1.27mm; LCSC C54668
U2: ATGM336H; LCSC C90770
U3: BL24C32F-RRRC; SOT-23-5; LCSC C5185883
U4: BME280; Bosch_LGA-8_2.5x2.5mm_P0.65mm_ClockwisePinNumbering; LCSC C92489
U5: DSK321STD; Oscillator_SMD_EuroQuartz_XO32-4Pin_3.2x2.5mm; LCSC C383430
U6: CJ6206B18M; SOT-23-5; LCSC C2829375
U7: ICM-20948; InvenSense_QFN-24_3x3mm_P0.4mm; LCSC C726001
U8: ATSAMD21G18A-A; TQFP-48_7x7mm_P0.5mm; LCSC C78624
U9: XC6206P332MR-G; SOT-23-3; LCSC C5446
U10: Ra-01; Ai-Thinker-Ra-01-LoRa; LCSC C2830750

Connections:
+BATT: J2.1, J7.1, JP1.2 (B), R16.1, SW3.3 (C)
A1: J1.9, U8.7 (PB08)
A2: U8.8 (PB09)
A3: U8.9 (PA04)
A4: U8.10 (PA05)
A5: U8.47 (PB02)
AREF: U8.4 (PA03)
BATT: C21.1, R15.1, R16.2, U8.3 (PA02)
BTN: J3.2, U8.13 (PA08)
CS: U8.22 (PA13), U10.15 (~NSS)
D2: J1.8, U8.23 (PA14)
D3: J1.4, U8.14 (PA09)
D+: J4.A6 (D+), J4.B6 (D+), U8.34 (PA25)
D-: J4.A7 (D-), J4.B7 (D-), U8.33 (PA24)
DIO0: U8.24 (PA15), U10.5 (DIO0)
ERR: R14.2, U8.28 (PA19)
GND: AE1.2 (GND), BT1.2 (-), C1.1, C2.1, C3.2, C4.1, C5.2, C7.2, C8.2, C9.2, C10.2, C11.2, C12.1, C13.2, C14.2, C15.2, C16.2, C17.2, C18.2, C19.2, C20.1, C21.2, C22.2, C23.2, C24.2, D1.1 (K), D2.1 (K), D3.1 (K), J1.1, J2.4, J3.1, J4.A1 (GND), J4.A12 (GND), J4.B1 (GND), J4.B12 (GND), J5.3, J5.5, J7.2, L1.2, Q3.1 (S), Q4.1 (S), R9.2, R11.2, R15.2, R17.2, R18.2, SW2.1, U1.1 (A0), U1.2 (A1), U1.3 (A2), U1.4 (GND), U1.7 (WP), U2.1 (GND), U2.10 (GND), U2.12 (GND), U3.2 (GND), U3.5 (WP), U4.1 (GND), U4.5 (SDO), U4.7 (GND), U5.2 (GND), U6.2 (GND), U7.18 (GND), U7.20 (RESV_GND), U8.5 (GNDANA), U8.18 (GND), U8.35 (GND), U8.42 (GND), U9.1 (GND), U10.2 (GND), U10.9 (GND), U10.16 (GND)
GPS: AE1.1 (FEED), L1.1, U2.11 (RF_IN)
GPS_EN: U2.5 (EN), U8.25 (PA16)
GPS_RST: U2.9 (RESET)
GPS_SCL: R5.1, U2.17 (SCL), U3.1 (SCL)
GPS_SDA: R1.1, U2.16 (SDA), U3.3 (SDA)
LED: R10.2, U8.26 (PA17)
LEFT: J9.3, U8.27 (PA18)
LORA_RST: U8.29 (PA20), U10.4 (~RESET)
L_FET: R20.2, U8.11 (PA06)
MISO: J1.7, U8.21 (PA12), U10.13 (MISO)
MOSI: J1.5, U8.19 (PB10), U10.14 (MOSI)
unnamed: AE2.1, U10.1 (ANT)
unnamed: D1.2 (A), R2.1
unnamed: D2.2 (A), R10.1
unnamed: D3.2 (A), R14.1
unnamed: J4.A5 (CC1), R11.1
unnamed: J4.B5 (CC2), R9.1
unnamed: J8.1, Q3.3 (D)
unnamed: J9.1, Q4.3 (D)
unnamed: Q3.2 (G), R17.1, R19.1
unnamed: Q4.2 (G), R18.1, R20.1
unnamed: C2.2, SW1.2 (B), U1.8 (VCC)
unnamed: C6.2, U5.3 (SIG)
unnamed: C11.1, U7.10 (REGOUT)
unnamed: C15.1, U8.43 (VDDCORE)
PPS: R2.2, U2.4 (PPS)
RESET: J5.10, R6.2, SW2.2, U8.40 (~RESET)
RIGHT: J8.3, U8.12 (PA07)
RX: U2.3 (RXD), U8.16 (PA11)
R_FET: R19.2, U8.30 (PA21)
SCK: J1.6, U8.20 (PB11), U10.12 (SCK)
SCL: J1.3, Q2.3 (D), R4.2, R13.1, U1.6 (SCL), U4.4 (SCK), U8.32 (PA23)
SCL_L: Q2.2 (S), R8.2, U7.23 (SCL/SCLK)
SDA: J1.2, Q1.3 (D), R3.2, R12.1, U1.5 (SDA), U4.3 (SDI), U8.31 (PA22)
SDA_L: Q1.2 (S), R7.2, U7.24 (SDA/MOSI)
SWCLK: J5.4, U8.45 (PA30)
SWDIO: J5.2, U8.46 (PA31)
TX: U2.2 (TXD), U8.15 (PA10)
USB_IN: C17.1, J4.A4 (VBUS), J4.A9 (VBUS), J4.B4 (VBUS), J4.B9 (VBUS), SW3.1 (A)
VCC: C20.2, C23.1, C24.1, J2.2, J8.2, J9.2, JP1.1 (A), SW3.2 (B), U9.3 (VI)
V_BAT: BT1.1 (+), U2.6 (VBAT)
XIN: C6.1, U8.1 (PA00)

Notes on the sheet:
Power switch
32.768 kHz TCXO
Reset circuit
512 KB EEPROM
Other circuitry and parts
Signal headers
Right servo and FET
GPS Module
J Link
Sensors/peripherals
LoRa module
Left servo and FET
USB-C (data and power)
Power
Indicator LEDs
BME280 (Humidity/Temp/Pressure)
IMU - ICM-20948
I2C pullup resistors
Linear reg
Mounting holes
Power headers
Power meter
SAMD

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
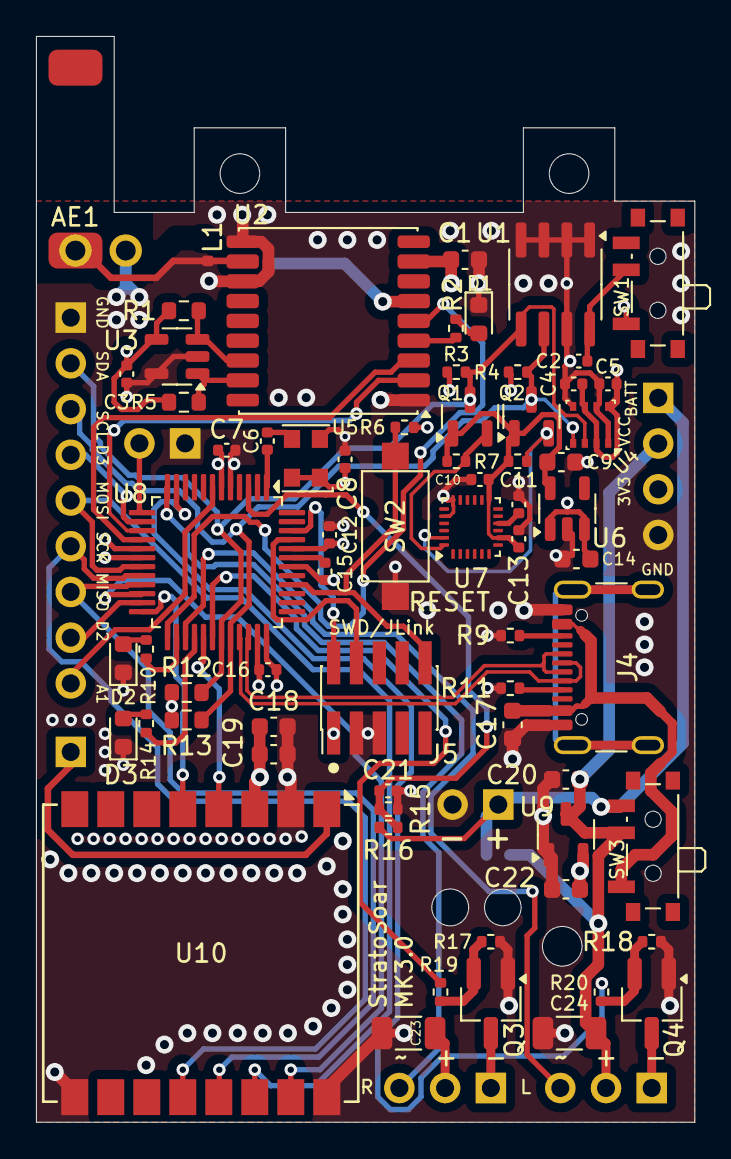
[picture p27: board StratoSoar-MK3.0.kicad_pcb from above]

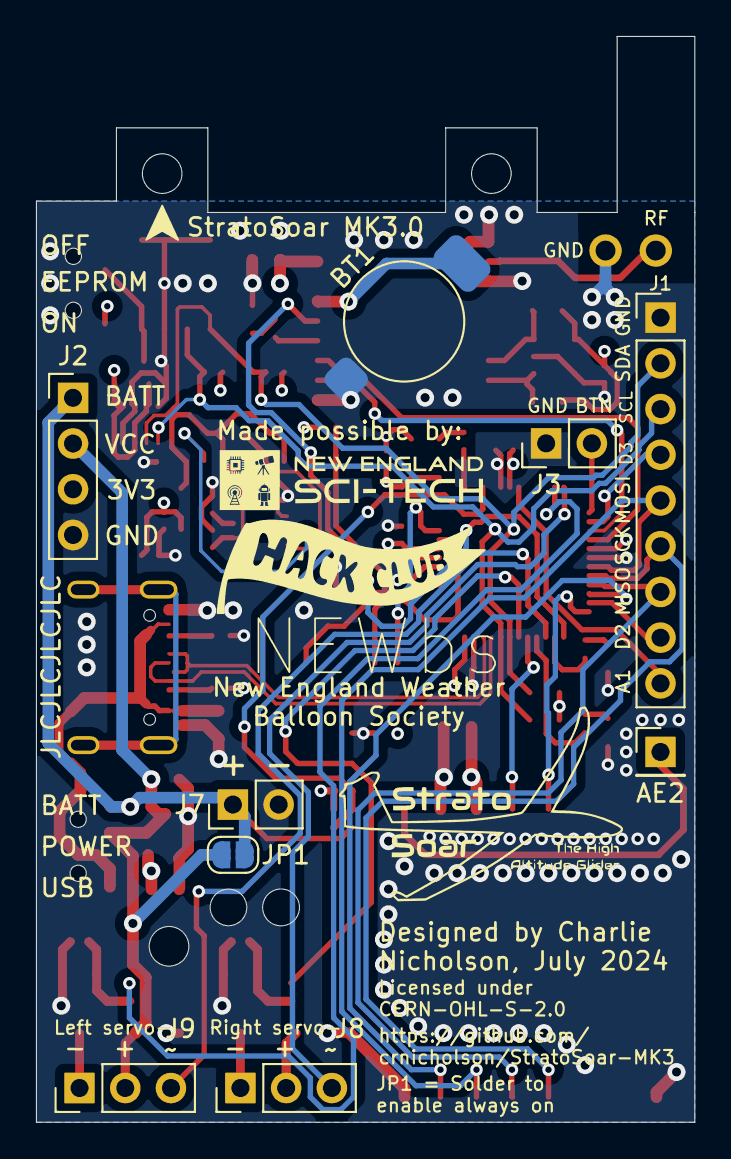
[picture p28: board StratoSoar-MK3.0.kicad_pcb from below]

Board: 4 copper layers, 36.6 x 60.3 mm, 81 parts (9 on the bottom side), 55 nets.

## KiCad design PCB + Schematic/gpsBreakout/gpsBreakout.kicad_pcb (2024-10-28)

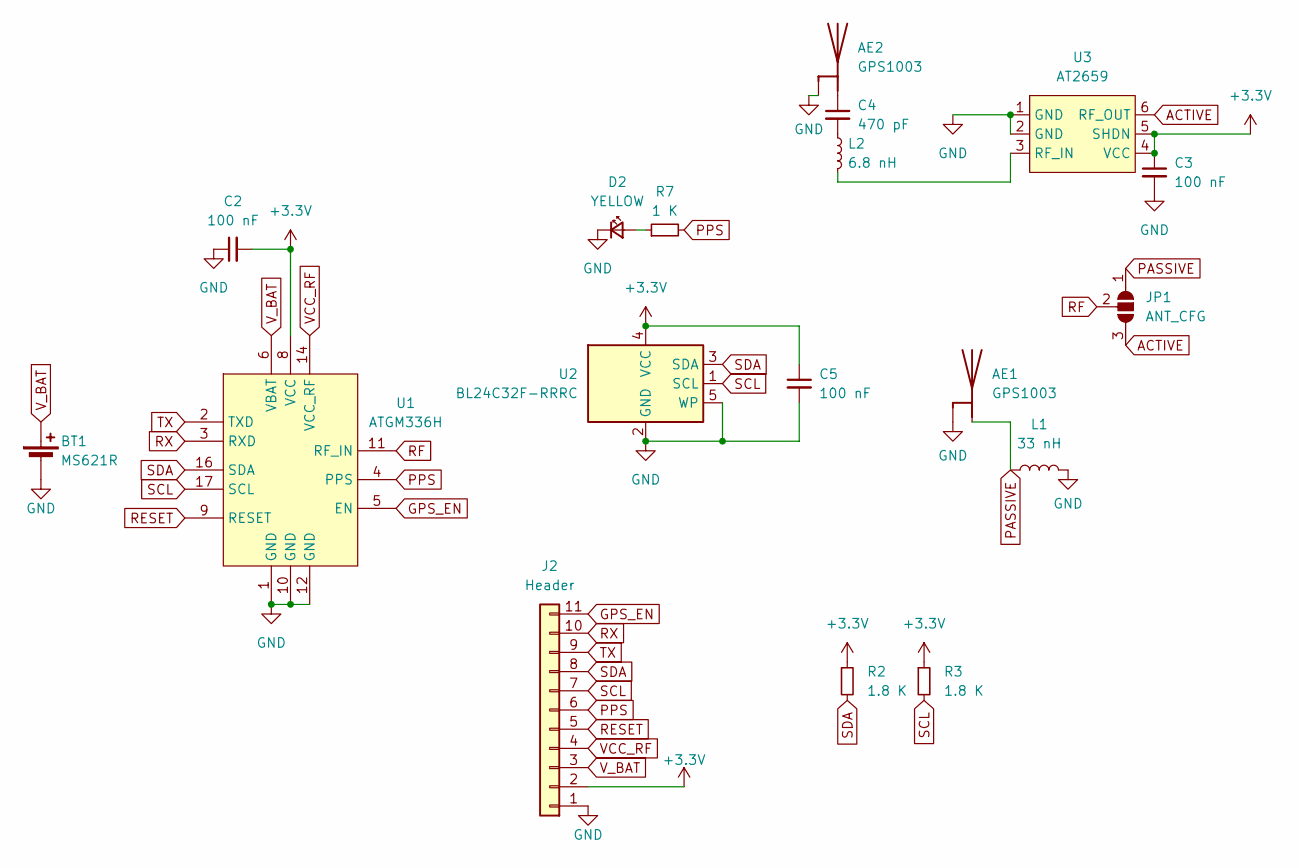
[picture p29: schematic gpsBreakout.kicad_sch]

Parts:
AE1, AE2: GPS1003
BT1: MS621R
C2, C3, C5: 100 nF; C_0603_1608Metric; LCSC C14663
C4: 470 pF; C_0402_1005Metric; LCSC C1567
D2: YELLOW; LED_0603_1608Metric; LCSC C72038
J2: Header; PinHeader_1x11_P2.54mm_Vertical
JP1: ANT_CFG; SolderJumper-3_P1.3mm_Open_RoundedPad1.0x1.5mm
L1: 33 nH; L_0402_1005Metric; LCSC C90178
L2: 6.8 nH; L_0402_1005Metric; LCSC C84403
R2, R3: 1.8 K; R_0603_1608Metric; LCSC C4177
R7: 1 K; R_0402_1005Metric; LCSC C11702
U1: ATGM336H; LCSC C90770
U2: BL24C32F-RRRC; SOT-23-5; LCSC C5185883
U3: AT2659; DFN150X100X80-6N; LCSC C92450

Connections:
+3.3V: C2.2, C3.1, C5.1, J2.2, R2.1, R3.1, U1.8 (VCC), U2.4 (VCC), U3.4 (VCC), U3.5 (SHDN)
ACTIVE: JP1.3 (B), U3.6 (RF_OUT)
GND: AE1.2 (GND), AE2.2 (GND), BT1.2 (-), C2.1, C3.2, C5.2, D2.1 (K), J2.1, L1.2, U1.1 (GND), U1.10 (GND), U1.12 (GND), U2.2 (GND), U2.5 (WP), U3.1 (GND), U3.2 (GND)
GPS_EN: J2.11, U1.5 (EN)
unnamed: AE2.1 (FEED), C4.1
unnamed: C4.2, L2.1
unnamed: D2.2 (A), R7.1
unnamed: L2.2, U3.3 (RF_IN)
PASSIVE: AE1.1 (FEED), JP1.1 (A), L1.1
PPS: J2.6, R7.2, U1.4 (PPS)
RESET: J2.5, U1.9 (RESET)
RF: JP1.2 (C), U1.11 (RF_IN)
RX: J2.10, U1.3 (RXD)
SCL: J2.7, R3.2, U1.17 (SCL), U2.1 (SCL)
SDA: J2.8, R2.2, U1.16 (SDA), U2.3 (SDA)
TX: J2.9, U1.2 (TXD)
VCC_RF: J2.4, U1.14 (VCC_RF)
V_BAT: BT1.1 (+), J2.3, U1.6 (VBAT)

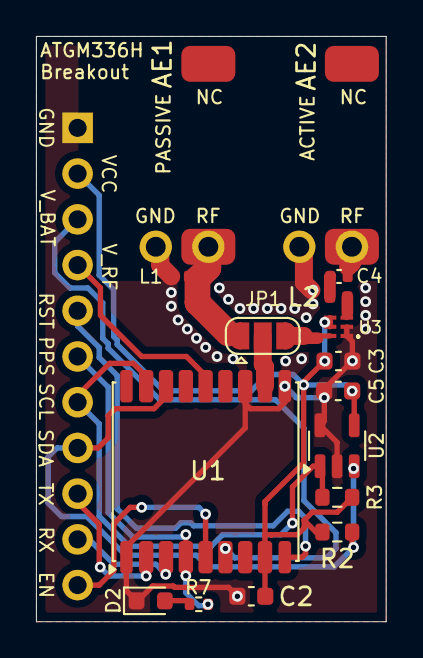
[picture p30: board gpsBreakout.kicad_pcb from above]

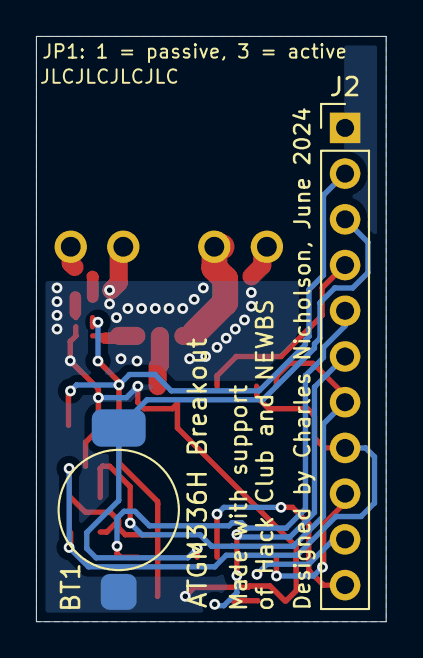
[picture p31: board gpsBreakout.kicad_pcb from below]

Board: 2 copper layers, 19.4 x 32.5 mm, 18 parts (2 on the bottom side), 18 nets.

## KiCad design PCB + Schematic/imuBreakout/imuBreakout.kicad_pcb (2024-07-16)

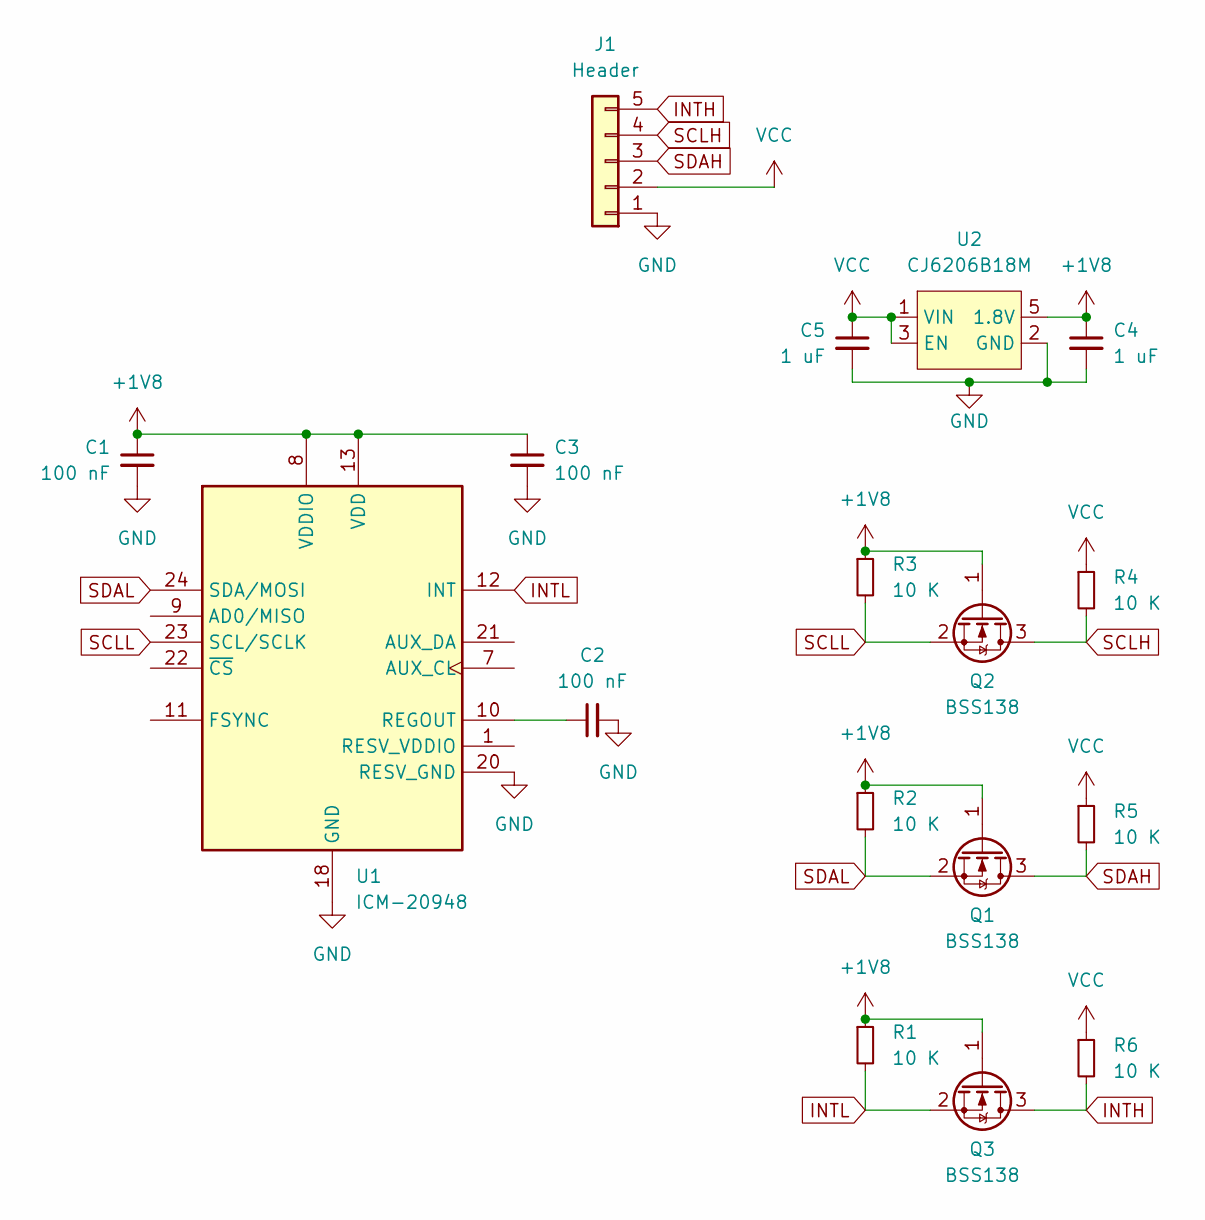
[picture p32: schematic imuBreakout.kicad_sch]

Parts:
C1, C2, C3: 100 nF; C_0402_1005Metric; LCSC C1525
C4, C5: 1 uF; C_0402_1005Metric; LCSC C52923
J1: Header; PinHeader_1x05_P2.54mm_Vertical
Q1, Q2, Q3: BSS138; SOT-23; LCSC C5224268
R1, R2, R3, R4, R5, R6: 10 K; R_0402_1005Metric; LCSC C25744
U1: ICM-20948; InvenSense_QFN-24_3x3mm_P0.4mm; LCSC C726001
U2: CJ6206B18M; SOT-23-5; LCSC C2829375

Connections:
+1V8: C1.1, C3.1, C4.1, Q1.1 (G), Q2.1 (G), Q3.1 (G), R1.1, R2.1, R3.1, U1.8 (VDDIO), U1.13 (VDD), U2.5 (1.8V)
GND: C1.2, C2.2, C3.2, C4.2, C5.2, J1.1, U1.18 (GND), U1.20 (RESV_GND), U2.2 (GND)
INTH: J1.5, Q3.3 (D), R6.2
INTL: Q3.2 (S), R1.2, U1.12 (INT)
unnamed: C2.1, U1.10 (REGOUT)
SCLH: J1.4, Q2.3 (D), R4.2
SCLL: Q2.2 (S), R3.2, U1.23 (SCL/SCLK)
SDAH: J1.3, Q1.3 (D), R5.2
SDAL: Q1.2 (S), R2.2, U1.24 (SDA/MOSI)
VCC: C5.1, J1.2, R4.1, R5.1, R6.1, U2.1 (VIN), U2.3 (EN)

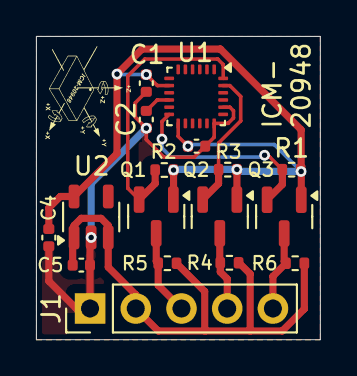
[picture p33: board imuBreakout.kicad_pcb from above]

Board: 2 copper layers, 15.8 x 16.8 mm, 17 parts (0 on the bottom side), 10 nets.

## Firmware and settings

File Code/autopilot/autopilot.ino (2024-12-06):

/*
autopilot.ino, part of StratoSoar MK3, for an autonomous glider.
Copyright (C) 2024 Charles Nicholson

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
You should have received a copy of the GNU General Public License
along with this program.  If not, see <https://www.gnu.org/licenses/>.
*/

// To-do:
// - Add correct flying wing dynamics
// - Test bi directional communication
// - Compile with different enables
// - Add a minimum temeperature for the cutdown mechanism
// - Add a flare on landing
// - Finish the SD card code
// - Take photos at certain areas
// - Add better turning with beizer for the waypoints

#include "blink.h"
#include "bme280.h"
#include "calc.h"
#include "eeprom.h"
#include "gps.h"
#include "i2c_scan.h"
#include "imu.h"
#include "lora.h"
#include "misc.h"
#include "servo.h"
#include "settings.h"
#include "vars.h"
#include "waypoint.h"
#include <Scheduler.h>

// Below are global variables. If you edit these, you'll need to edit vars.h as well.

// GPS vars.
float lat, lon, altitude, targetLat = TARGET_LAT, targetLon = TARGET_LON, hdop;
int year, month, day, hour, minute, second, gpsLast;

// Navigation/IMU vars.
int turnAngle, servoPositionLeft, servoPositionRight, servoPositionRudder, servoPositionElevator, distance;
float yaw, pitch, roll;

// Environmental vars.
float temperature, pressure, bmeAltitude;
int humidity;

// Other vars.
int lastLoRa, loraUpdateRate = LORA_UPDATE_RATE, updateRate = UPDATE_RATE, lastUpdate;
bool abortFlight, altitudeLock, lowVoltage, ultraLowVoltage;
float desiredPitch = DESIRED_PITCH, voltage;

struct data toGliderStruct;

void setup() {
  pinMode(GPS_SLEEP_PIN, OUTPUT);
  pinMode(LED, OUTPUT);
  pinMode(ERR_LED, OUTPUT);
  pinMode(LEFT_FET, OUTPUT);
  pinMode(RIGHT_FET, OUTPUT);
  pinMode(LORA_RESET_PIN, OUTPUT);
  pinMode(DIO0_PIN, OUTPUT);
  pinMode(VOLTMETER_PIN, INPUT);
  digitalWrite(GPS_SLEEP_PIN, HIGH); // GPS on for default.
  digitalWrite(LED, LOW);
  digitalWrite(ERR_LED, LOW);
  digitalWrite(LEFT_FET, LOW);  // Servo off for default.
  digitalWrite(RIGHT_FET, LOW); // Servo off for default.

  longBlink(LED);     // Show startup.
  longBlink(ERR_LED); // Show startup.

#ifdef DEVMODE
  SerialUSB.begin(BAUD_RATE);
  while (!SerialUSB)
    longBlink(ERR_LED);
  SerialUSB.println("StratoSoar MK3.0 Autopilot.");
#endif

  longBlink(LED); // Show successful serial init.

  Wire.begin();
  imuSetup();
  servoSetup();
#ifdef USE_EEPROM
  eepromSetup();
#endif
#ifdef USE_LORA
  loraSetup();
#endif
#ifdef USE_BME
  if (findDevice(0x77) || findDevice(0x76)) {
#ifdef DEVMODE
    SerialUSB.println("BME280 has been found.");
#endif
    if (findDevice(0x77))
      BME280setI2Caddress(119);
    if (findDevice(0x76))
      BME280setI2Caddress(118);
  } else {
#ifdef DEVMODE
    SerialUSB.println("BME280 has not been found. Freezing sketch.");
#endif
    while (1)
      longBlink(ERR_LED);
  }
#endif
#ifdef USE_GPS
#ifdef DEVMODE
  SerialUSB.println("Setting up GPS and waiting for a fix. This may take a while.");
#endif
  gpsSetup();
  waitForFix();
#endif
#ifdef USE_WAYPOINTS
  waypointsSetup();
#endif

#ifndef USE_GPS
  lat = TESTING_LAT, lon = TESTING_LON;
#endif

#ifdef DEVMODE
  SerialUSB.println("Testing servos...");
#endif
#ifdef FLYING_WING
  moveLeftServo(90);
  moveRightServo(90);
  moveLeftServo(0);
  moveRightServo(0);
  moveLeftServo(90);
  moveRightServo(90);
#endif
#ifndef FLYING_WING
  moveRudder(90);
  moveElevator(90);
  moveRudder(0);
  moveElevator(0);
  moveRudder(90);
  moveElevator(90);
#endif

#ifdef FIND_PITCH
#ifndef USE_BME
#error "Please enable BME to find the optimum pitch."
#ifdef DEVMODE
  SerialUSB.println("Please enable BME to find the optimum pitch.");
#endif
  while (1) {
    longBlink(ERR_LED);
  }
#endif
#ifndef USE_GPS
#error "Please enable GPS to find the optimum pitch."
#ifdef DEVMODE
  SerialUSB.println("Please enable GPS to find the optimum pitch.");
#endif
  while (1) {
    longBlink(ERR_LED);
  }
#endif
#ifdef DEVMODE
  SerialUSB.print("Starting the optimum pitch finder program. Please drop the glider for ");
  SerialUSB.print(PITCH_RANGE * PITCH_STEPS * STEP_TIME);
  SerialUSB.println(" plus an additional 15 seconds for the glider to get up to speed.");
#endif
  desiredPitch = findBestPitch();
#endif

  Scheduler.startLoop(loop1);
#ifdef USE_GPS
  Scheduler.startLoop(loop2);
#endif
#ifdef USE_LORA
  Scheduler.startLoop(loop3);
#endif

#ifdef DEVMODE
  SerialUSB.println("Everything has initialized, moving on to main sketch.");
#endif
}

void loop() { // We're doing threading on an Arduino! (This is a really cool library).
  imuMath();  // This runs in the background 24/7. When the code is ready to access the data, getAHRS() is called.
  yield();
}

void loop1() {
#ifdef DROP_START
  int altitudeCounter = 0;
  float lastAltitude = 0;
  while (bmeAltitude < LOCK_ALTITUDE) {
    getBMEData(SEA_LEVEL_PRESSURE); // Get BME data, put into global variables.
#ifdef DEVMODE
    SerialUSB.println("Waiting to initiate flight until the lock altitude is reached.");
#endif
    delay(1000);
  }
  while (altitudeCounter < 2) {
    lastAltitude = bmeAltitude;
    getBMEData(SEA_LEVEL_PRESSURE); // Get BME data, put into global variables.
    if (bmeAltitude < lastAltitude) {
      altitudeCounter++;
    }
#ifdef DEVMODE
    SerialUSB.println("Waiting until the altitude is dropping for two times in a row.");
#endif
    delay(1000);
  }
  moveLeftServo(90);
  moveRightServo(90);
  delay(1000);
  moveLeftServo(95);
  moveRightServo(95);
  delay(5000); // Give enough time for the glider to stabilize in flight before starting steering shenanigans.
#endif

#ifdef SERVO_NONBLOCKING
#ifdef FLYING_WING
  updateLeftServo();
  updateRightServo();
#endif
#ifndef FLYING_WING
  updateRudder();
  updateElevator();
#endif
#endif

  if (millis() - lastUpdate > updateRate) {
    getAHRS(); // Get the yaw, pitch, and roll from the IMU and assign it the respective global variables.

    // Getting sensor values.
#ifdef USE_BME
    getBMEData(SEA_LEVEL_PRESSURE); // Get BME data, put into global variables.
#endif

    // Calculations.
    distance = calculateDistance(lat, lon, targetLat, targetLon);
    turnAngle = turningAngle(lat, lon, yaw, targetLat, targetLon);

#ifdef USE_VOLTAGE
    voltage = readVoltage();
#endif
#ifndef USE_VOLTAGE
    voltage = (LOW_VOLTAGE + 0.1) * 2; // Fake the voltage if reader is disabled.
#endif
    if (voltage < LOW_VOLTAGE) {
      lowVoltage = true;
      updateRate = 5000;      // Move the servos less frequently.
      loraUpdateRate = 30000; // Reduce the LoRa update rate.
    }
    if (voltage < TOO_LOW_VOLTAGE) {
      ultraLowVoltage = true;
      loraUpdateRate = 60000; // Reduce the LoRa update rate even further.
      abortFlight = true;     // Land the glider.
    }

#ifdef USE_WAYPOINTS
    if (!lowVoltage) {
      updateWaypoint(); // Update the target lat and lon if waypoints are enabled.
    }
#endif

    // Landing.
    if (altitude > LOCK_ALTITUDE) {
      altitudeLock = true; // This enables when the glider is above a certain altitude. This makes sure it doesn't land when we're releasing it.
    }
    if (altitude < LAND_ALTITUDE + TARGET_ALT && altitudeLock) {
      abortFlight = true;
    }
    if (abortFlight) {
      getNextCircleWaypoint(lat, lon, 30); // Experimental. Get new targetLat and targetLon which sends glider into a spiral.
    }

    // Calculate again if needed.
    if (abortFlight) {
      distance = calculateDistance(lat, lon, targetLat, targetLon);
      turnAngle = turningAngle(lat, lon, yaw, targetLat, targetLon);
    }

#ifdef FLYING_WING
    pidElevons(pitch, turnAngle); // Get servoPositionLeft, servoPositionRight.
#ifdef SERVO_NONBLOCKING
    startLeftServo(servoPositionLeft);
    startRightServo(servoPositionRight);
#endif
#ifndef SERVO_NONBLOCKING
    moveLeftServo(servoPositionLeft);
    moveRightServo(servoPositionRight);
#endif
#endif
#ifndef FLYING_WING
    servoPositionRudder = pidRudder(turnAngle);
    servoPositionElevator = pidElevator(pitch);
#ifdef SERVO_NONBLOCKING
    startRudder(servoPositionRudder);
    startElevator(servoPositionElevator);
#endif
#ifndef SERVO_NONBLOCKING
    moveRudder(servoPositionRudder);
    moveElevator(servoPositionElevator);
#endif
#endif

    // EEPROM.
#ifdef USE_EEPROM
    writeDataToEEPROM(lat, lon, altitude, yaw, pitch, roll, hour, minute, second); // Write all the data to EEPROM.
#endif

#ifdef DEVMODE
#ifdef DISPLAY_DATA
    printData(); // Print all the data to the serial monitor.
#endif
#endif

    lastUpdate = millis();
  }
  yield();
}

#ifdef USE_GPS
void loop2() {
  // If not using GPS low power, just get data and do nothing else.
#ifndef GPS_LOW_POWER
  if (millis() - gpsLast > GPS_UPDATE_RATE) {
    gpsLast = millis();
    getGPSData(); // Get GPS data. If data is invalid, it waits for a better fix.
  }
#endif
  // If using GPS low power mode, get data and put GPS to sleep.
#ifdef GPS_LOW_POWER
  if (millis() - gpsLast > GPS_LOW_POWER_RATE) {
    gpsLast = millis();
    gpsWakeup();  // Wakeup GPS module and wait for fix.
    getGPSData(); // Get GPS data and put into global variables.
    gpsSleep();   // Put GPS module to sleep.
  }
#endif
  yield();
}
#endif

#ifdef USE_LORA
void loop3() {
#ifdef FAST_LORA
  toGliderStruct.lat = lat;
  toGliderStruct.lon = lon;
  toGliderStruct.tLat = targetLat;
  toGliderStruct.tLon = targetLon;
  toGliderStruct.altitude = altitude;
  toGliderStruct.temperature = temperature;
  toGliderStruct.pressure = pressure;
  toGliderStruct.humidity = humidity;
  toGliderStruct.volts = voltage;
  toGliderStruct.yaw = yaw;
  toGliderStruct.pitch = pitch;
  toGliderStruct.roll = roll;
  toGliderStruct.year = year;
  toGliderStruct.month = month;
  toGliderStruct.day = day;
  toGliderStruct.hour = hour;
  toGliderStruct.minute = minute;
  toGliderStruct.second = second;
  toGliderStruct.txCount++;
  toGliderStruct.abortFlight = abortFlight;
  sendData(toGliderStruct);
  lastLoRa = millis();
#endif
#ifndef FAST_LORA
  if (millis() - lastLoRa > loraUpdateRate) {
    toGliderStruct.lat = lat;
    toGliderStruct.lon = lon;
    toGliderStruct.tLat = targetLat;
    toGliderStruct.tLon = targetLon;
    toGliderStruct.altitude = altitude;
    toGliderStruct.temperature = temperature;
    toGliderStruct.pressure = pressure;
    toGliderStruct.humidity = humidity;
    toGliderStruct.volts = voltage;
    toGliderStruct.yaw = yaw;
    toGliderStruct.pitch = pitch;
    toGliderStruct.roll = roll;
    toGliderStruct.year = year;
    toGliderStruct.month = month;
    toGliderStruct.day = day;
    toGliderStruct.hour = hour;
    toGliderStruct.minute = minute;
    toGliderStruct.second = second;
    toGliderStruct.txCount++;
    toGliderStruct.abortFlight = abortFlight;
#ifdef HAMMING
    sendHammingData(toGliderStruct); // Sends with forward error correction for redundancy over long distances.
#endif
#ifndef HAMMING
    normalSend(); // Sends without forward error correction.
#endif
    lastLoRa = millis();
#endif
  }
#ifdef HAMMING
  hammingReceive(); // Receive LoRa data to abort flight or change targetLat and targetLon.
#endif
#ifndef HAMMING
  normalReceive(); // Receive LoRa data to abort flight or change targetLat and targetLon.
#endif
}
#endif

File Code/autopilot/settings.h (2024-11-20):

/*
settings.h, part of StratoSoar MK3, for an autonomous glider.
Copyright (C) 2024 Charles Nicholson

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
You should have received a copy of the GNU General Public License
along with this program. If not, see <https://www.gnu.org/licenses/>.
*/

#pragma once

// Enables.
#define DEVMODE // Toggle serial monitor.
// #define GPS_LOW_POWER // Sets the GPS to sleep after waking up after every GPS_LOW_POWER_RATE milliseconds.
// #define USE_GPS
// #define USE_BME
// #define USE_EEPROM
// #define USE_LORA
// #define USE_VOLTAGE
#define FAST_LORA // Ignore other LoRa settings and use a very quick LoRa update rate for short range.
// #define USE_WAYPOINTS
// #define SMOOTH_TURNING // Smoothly turn the glider towards the next waypoint.
// #define FIND_PITCH // Use a program to find the best pitch of the glider. BME and GPS must be enabled. Very experimental.
// #define DROP_START // Don't start the program until the glider has detected a drop in altitude.
#define DISPLAY_DATA // Dump the data on the serial monitor every update.
// #define FLYING_WING  // If enabled, the glider uses flying wing kinematics. If not, it uses the traditional rudder and elevator.
// #define SERVO_NONBLOCKING // Use non-blocking code for the servo.
// #define HAMMING // Use hamming encoding for the LoRa data.

// Pins.
#define LED 13
#define ERR_LED 12
#define GPS_SLEEP_PIN 11
#define LEFT_SERVO 10
#define RUDDER_PIN 10
#define RIGHT_SERVO 9
#define ELEVATOR_PIN 9
#define LEFT_FET 8
#define RUDDER_FET 8
#define RIGHT_FET 7
#define ELEVATOR_FET 7
#define LORA_RESET_PIN 6
#define DIO0_PIN 5
// #define BUTTON 4   // Reserved for future use.
// #define RESERVED 1 // Reserved for serial GPS connection.
// #define RESERVED 0 // Reserved for serial GPS connection.
#define SS_PIN 38
#define VOLTMETER_PIN A0

// Pins broken out.
// #define SDA     // Physical pin 31
// #define SCL     // Physical pin 32
// #define MOSI    // Physical pin 19
// #define MISO    // Physical pin 21
// #define SCK     // Physical pin 20
// #define GPIO 3  // Physical pin 14
// #define GPIO 2  // Physical pin 23
// #define GPIO A1 // Physical pin 7

// Other.
#define UPDATE_RATE 1000           // The time in milliseconds between glider respositionings.
#define BAUD_RATE 115200           // Baud rate of the serial monitor.
#define SEA_LEVEL_PRESSURE 1013.25 // Sea level pressure in hPa.
#define DECLINATION 0              // -13.5          // Local magnetic declination in degrees in Boston. Yaw increases CW from North. Can be found here: https://www.ngdc.noaa.gov/geomag-web/#declination.
#define AD0_VAL 0                  // Change I2C address of IMU. 0 = 0x68, 1 = 0x69.
#define LAND_ALTITUDE 100          // This many meters from the gorund the glider will start its landing sequence.
#define LOCK_ALTITUDE 1000         // The landing sequence will only be available after this many meters in altitude.
#define CHANGE_WAYPOINT 10         // The distance in meters between the current location and the waypoint needed before changing to the next waypoint.
#define LOW_VOLTAGE 3.2            // Below this voltage the glider will reduce the frequency of position updates and servo updates.
#define TOO_LOW_VOLTAGE 3.0        // Below this voltage the glider will simply spiral down with even fewer updates.

// Glider pitch control.
#define DESIRED_PITCH -5.0 // Pitch the glider should be flying at during the flight.
#define STARTING_PITCH -6  // The pitch the glider starts at before finding the best pitch.
#define PITCH_RANGE 4      // This many degrees will be added to the value of PITCH as the high value.
#define PITCH_STEPS 1      // This is the number of degrees stepped upwards when finding the optimum pitch angle per cycle.
#define STEP_TIME 10       // Time in seconds spent on each step.

#define SETPOINT_PITCH 0    // For the flying wing.
#define SETPOINT_ELEVATOR 0 // For the traditional setup.

// PID settings.
#define KP_LEFT 1
#define KI_LEFT 0
#define KD_LEFT 0

#define KP_RIGHT 1
#define KI_RIGHT 0
#define KD_RIGHT 0

#define KP_RUDDER 1
#define KI_RUDDER 0
#define KD_RUDDER 0

#define KP_ELEVATOR 1
#define KI_ELEVATOR 0
#define KD_ELEVATOR 0

// EEPROM.
// #define ERASE_EEPROM // Erases the EEPROM every start. Highly unreccomended.
#define EEPROM_SIZE 512    // Valid types: 0, 1, 2, 4, 8, 16, 32, 64, 128, 256, 512, 1025, 2048
#define BYTES_PER_CYCLE 19 // Number of bytes written to the EEPROM per cycle.
#define EEPROM_BUFFER 50   // Buffer in milliseconds for the frequency of EEPROM write cycles.
#define FLIGHT_TIME 180    // The estimated time in minutes of the flight, used in estimating the write cycle of the EEPROM.

// GPS.
#define GPS_BAUD_RATE 9600       // Baud rate of the GPS module.
#define GPS_UPDATE_RATE 1000     // The time in milliseconds stating the frequency of new GPS data. Cannot go lower than 1000 ms without chaning config on GPS.
#define GPS_LOW_POWER_RATE 15000 // The time in milliseconds stating the frequency of new GPS data in low power mode.
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

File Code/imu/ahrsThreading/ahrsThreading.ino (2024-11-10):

// Modified version of ICM-20948 AHRS code from SJ Remington.

// Calibration procedure can be found here: http://sailboatinstruments.blogspot.com/2011/08/improved-magnetometer-calibration.html

#include <ICM_20948.h> // You will need the Sparkfun ICM-20948 library.
#include <Scheduler.h>

// Settings.
#define DECLINATION 0    // -13.5 // Local magnetic declination in degrees in Boston. Yaw increases CW from North. Can be found here: https://www.ngdc.noaa.gov/geomag-web/#declination.
#define AD0_VAL 0        // Change I2C address. 0 = 0x68, 1 = 0x69.
#define PRINT_SPEED 1000 // The milliseconds between printouts.
#define BAUD_RATE 115200 // The baud rate for the serial monitor.
// #define HERTZ             // Print the frequency of the sensor.

// These are the previously determined offsets and scale factors for the accelerometer and magnetometer.
// Gyro default scale 250 dps. Convert to radians/sec subtract offsets
float Gscale = (M_PI / 180.0) * 0.00763; // 250 dps scale sensitivity = 131 dps/LSB
float G_offset[3] = {69.6, 22.0, -35.1};

float A_B[3]{774.57, 109.87, 821.08};

float A_Ainv[3][3]{{0.0602, -0.00097, -0.00513},
                   {-0.00097, 0.06405, -0.00172},
                   {-0.00513, -0.00172, 0.0561}};

float M_B[3]{15.29, 184.51, 37.83};

float M_Ainv[3][3]{{3.03796, -0.04154, -0.0047},
                   {-0.04154, 2.95127, -0.02467},
                   {-0.0047, -0.02467, 2.95456}};

// Don't change. Tuning parameters. IMU_KP is not yet optimized (slight overshoot apparent after rapid sensor reorientations). IMU_KI is not used.
#define IMU_KP 50.0
#define IMU_KI 0.0

// Variables.
unsigned long now, last; // For counting time between updates.
float deltat = 0;        // For counting time between updates in microseconds.

int hertz; // For measuring frequency of sensor.

unsigned long lastPrint = 0; // Keep track of print time

float q[4] = {1.0, 0.0, 0.0, 0.0};           // Vector to hold quaternion.
float yaw, pitch, roll;                      // Euler angle output.
float Gxyz[3], Axyz[3], Mxyz[3];             // Centered and scaled gyro/accel/mag data.
float integralError[3] = {0.0f, 0.0f, 0.0f}; // Integral error for Mahony method.
bool imuInit, magInit;                       // Bools for IMU and magnetometer initialization.å

ICM_20948_I2C imu; // Create the IMU object.

void setup() {
  SerialUSB.begin(BAUD_RATE);
  while (!SerialUSB)
    ;

  SerialUSB.println("ICM-20948 AHRS testing.");

  Wire.begin();
  Wire.setClock(400000);

  imuSetup();

  Scheduler.startLoop(loop1);

  delay(15000);
}

void loop() {
  imuMath();
  yield();
}

void loop1() {
  // Check to see if it's time to print out the data.
  if (millis() - lastPrint > PRINT_SPEED) {
    delay(50);
    outputAHRS();
  }
  yield();
}

void imuSetup() {
  while (!imuInit || !magInit) {
    imu.begin(Wire, AD0_VAL);

    SerialUSB.print("Initialization of the IMU returned: ");
    SerialUSB.println(imu.statusString());
    if (imu.status != ICM_20948_Stat_Ok) {
      SerialUSB.println("Trying again...");
      delay(500);
    } else {
      imuInit = true;
    }

    imu.startupMagnetometer();
    SerialUSB.print(F("Initialization of the magnetometer returned: "));
    SerialUSB.println(imu.statusString());
    if (imu.status != ICM_20948_Stat_Ok) {
      SerialUSB.println("Trying again...");
      delay(500);
    } else {
      magInit = true;
    }
  }

  SerialUSB.println("ICM-20948 connected. Sketch starting shortly.");
#ifdef HERTZ
  SerialUSB.println("Yaw, pitch, roll, Hertz");
#endif
#ifndef HERTZ
  SerialUSB.println("Yaw, pitch, roll");
#endif
}

void outputAHRS() {
  // Converting the quarternions to Euler angles (radians). This angular conversion can fail. See gimbal lock.
  roll = atan2((q[0] * q[1] + q[2] * q[3]), 0.5 - (q[1] * q[1] + q[2] * q[2]));
  pitch = asin(2.0 * (q[0] * q[2] - q[1] * q[3]));
  yaw = atan2((q[1] * q[2] + q[0] * q[3]), 0.5 - (q[2] * q[2] + q[3] * q[3]));

  // Converting radians to degrees.
  yaw *= 180.0 / PI;
  pitch *= 180.0 / PI;
  roll *= 180.0 / PI;

  // Accounting for declination.
  yaw = -(yaw + DECLINATION);
  if (yaw < 0)
    yaw += 360.0;
  if (yaw >= 360.0)
    yaw -= 360.0;

  SerialUSB.print(yaw, 0);
  SerialUSB.print(", ");
  SerialUSB.print(pitch, 0);
  SerialUSB.print(", ");
#ifdef HERTZ
  SerialUSB.print(roll, 0);
  SerialUSB.print(", ");
  SerialUSB.print(hertz / (PRINT_SPEED / 1000), 0); // Calculating the frequency of the sensor.
  SerialUSB.println(" Hz");
#endif
#ifndef HERTZ
  SerialUSB.println(roll, 0);
#endif

  hertz = 0; // Reset counter for next print.
  lastPrint = millis();
}

void imuMath() {
  if (imu.dataReady()) {
    imu.getAGMT(); // Get accelerometer, gyro, mag, and temperature data and put it into the imu.agmt data structure.

    hertz++;

    getScaledIMU(Gxyz, Axyz, Mxyz); // Scale the raw values of the IMU.

    Mxyz[1] = -Mxyz[1]; // Reflect Y and Z.
    Mxyz[2] = -Mxyz[2]; // Must be done after offsets & scales applied to raw data.

    now = micros();
    deltat = (now - last) * 1.0e-6; // Get microseconds since last update.
    last = now;

    quaternionUpdate(Axyz[0], Axyz[1], Axyz[2], Gxyz[0], Gxyz[1], Gxyz[2], Mxyz[0], Mxyz[1], Mxyz[2], deltat); // Updates the quaternion array with the scaled values.
  }
}

float vectorDot(float a[3], float b[3]) {
  return a[0] * b[0] + a[1] * b[1] + a[2] * b[2];
}

void vectorNormalize(float a[3]) {
  float mag = sqrt(vectorDot(a, a));
  a[0] /= mag;
  a[1] /= mag;
  a[2] /= mag;
}
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

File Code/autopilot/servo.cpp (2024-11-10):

/*
servo.cpp, part of StratoSoar MK3, for an autonomous glider.
Copyright (C) 2024 Charles Nicholson

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
You should have received a copy of the GNU General Public License
along with this program.  If not, see <https://www.gnu.org/licenses/>.
*/

#include "servo.h"

int prevErrorPitch, prevErrorYaw, integralPitch, integralYaw, leftTime, rightTime, rudderTime, elevatorTime, prevErrorRudder, integralRudder, prevErrorElevator, integralElevator;
unsigned long leftServoStartTime, rightServoStartTime, rudderStartTime, elevatorStartTime;
bool leftServoMoving, rightServoMoving, rudderMoving, elevatorMoving;

Servo leftServo, rightServo;
Servo rudder, elevator;

void servoSetup() {
#ifdef FLYING_WING
  leftServo.attach(LEFT_SERVO);
  rightServo.attach(RIGHT_SERVO);
#endif
#ifndef FLYING_WING
  rudder.attach(RUDDER_PIN);
  elevator.attach(ELEVATOR_PIN);
#endif
}

void pidElevons(int pitch, int turningAngle) {
  int errorPitch = SETPOINT_PITCH - pitch;

  int outputPitch = KP_LEFT * errorPitch + KI_LEFT * integralPitch + KD_LEFT * (errorPitch - prevErrorPitch);
  int outputYaw = KP_RIGHT * turningAngle + KI_RIGHT * integralYaw + KD_RIGHT * (turningAngle - prevErrorYaw);

  prevErrorPitch = errorPitch;
  integralPitch += errorPitch;

  prevErrorYaw = turningAngle;
  integralYaw += turningAngle;

  servoPositionLeft = 90 - outputPitch + outputYaw + desiredPitch;
  servoPositionRight = 90 - outputPitch - outputYaw + desiredPitch;

  // Map servo positions if needed.
  // servoPositionLeft = map(servoPositionLeft, 0, 180, 750, 2250);
  // servoPositionRight = map(servoPositionRight, 0, 180, 750, 2250);
}

int pidRudder(int turningAngle) {
  int outputRudder = KP_RUDDER * turningAngle + KI_RUDDER * integralRudder + KD_RUDDER * (turningAngle - prevErrorRudder);

  // Update previous error and integral.
  prevErrorRudder = turningAngle;
  integralRudder += turningAngle;

  // map(servoPositionRudder, 0, 180, 1250, 1750); // For servos that take microseconds, not degrees.

  return (180 + outputRudder) / 2;
}

int pidElevator(int pitch) {
  int errorElevator = SETPOINT_ELEVATOR - pitch; // Calculate the error.

  int outputElevator = KP_ELEVATOR * errorElevator + KI_ELEVATOR * integralElevator + KD_ELEVATOR * (errorElevator - prevErrorElevator);

  // Update previous error and integral.
  prevErrorElevator = errorElevator;
  integralElevator += errorElevator;

  // map(servoPositionElevator2, 0, 180, 750, 2250); // For servos that take microseconds, not degrees.

  return 90 - outputElevator;
}

void moveLeftServo(int degrees) {
  digitalWrite(LEFT_FET, HIGH); // Turn servo on.
  int leftLast = leftServo.read();
  int leftChange = abs(leftLast - degrees);
  int leftTime = leftChange * 170 / 60;
  if (leftTime < 40) {
    leftTime = leftTime + 40;
  }
  if (leftTime < 60) {
    leftTime = leftTime + 20;
  }
  leftServo.write(degrees);
  delay(leftTime);
  digitalWrite(LEFT_FET, LOW); // Turn servo off.
}

void startLeftServo(int degrees) {
  digitalWrite(LEFT_FET, HIGH); // Turn servo on.

  int leftChange = abs(leftServo.read() - degrees);
  leftTime = leftChange * 170 / 60;
  if (leftTime < 40) {
    leftTime += 40;
  }
  if (leftTime < 60) {
    leftTime += 20;
  }

  leftServo.write(degrees);
  leftServoStartTime = millis();
  leftServoMoving = true;
}

void updateLeftServo() {
  if ((millis() - leftServoStartTime > leftTime) && leftServoMoving) {
    digitalWrite(LEFT_FET, LOW);
    leftServoMoving = false;
  }
}

void moveRightServo(int degrees) {
  digitalWrite(RIGHT_FET, HIGH); // Turn servo on.
  int rightLast = rightServo.read();
  int rightChange = abs(rightLast - degrees);
  int rightTime = rightChange * 170 / 60;
  if (rightTime < 40) {
    rightTime = rightTime + 40;
  }
  if (rightTime < 60) {
    rightTime = rightTime + 20;
  }
  rightServo.write(degrees);
  delay(rightTime);
  digitalWrite(RIGHT_FET, LOW); // Turn servo off.
}

void startRightServo(int degrees) {
  digitalWrite(RIGHT_FET, HIGH); // Turn servo on.

  int rightChange = abs(rightServo.read() - degrees);
  rightTime = rightChange * 170 / 60;
  if (rightTime < 40) {
    rightTime += 40;
  }
  if (rightTime < 60) {
    rightTime += 20;
  }

  rightServo.write(degrees);
  rightServoStartTime = millis();
  rightServoMoving = true;
}

void updateRightServo() {
  if ((millis() - rightServoStartTime > rightTime) && rightServoMoving) {
    digitalWrite(RIGHT_FET, LOW);
    rightServoMoving = false;
  }
}

void moveRudder(int degrees) {
  digitalWrite(RUDDER_FET, HIGH); // Turn servo on.
  int rudderLast = rudder.read();
  int rudderChange = abs(rudderLast - degrees);
  int rudderTime = rudderChange * 170 / 60;
  if (rudderTime < 40) {
    rudderTime = rudderTime + 40;
  }
  if (rudderTime < 60) {
    rudderTime = rudderTime + 20;
  }
  rudder.write(degrees);
  delay(rudderTime);
  digitalWrite(RUDDER_FET, LOW); // Turn servo off.
}

void startRudder(int degrees) {
  digitalWrite(RUDDER_FET, HIGH); // Turn servo on.

  int rudderChange = abs(rudder.read() - degrees);
  rudderTime = rudderChange * 170 / 60;
  if (rudderTime < 40) {
    rudderTime += 40;
  }
  if (rudderTime < 60) {
    rudderTime += 20;
  }

  rudder.write(degrees);
  rudderStartTime = millis();
  rudderMoving = true;
}

void updateRudder() {
  if ((millis() - rudderStartTime > rudderTime) && rudderMoving) {
    digitalWrite(RIGHT_FET, LOW);
    rudderMoving = false;
  }
}

void moveElevator(int degrees) {
  digitalWrite(ELEVATOR_FET, HIGH); // Turn servo on.
  int elevatorLast = elevator.read();
  int elevatorChange = abs(elevatorLast - degrees);
  int elevatorTime = elevatorChange * 170 / 60;
  if (elevatorTime < 40) {
    elevatorTime = elevatorTime + 40;
  }
  if (elevatorTime < 60) {
    elevatorTime = elevatorTime + 20;
  }
  elevator.write(degrees);
  delay(elevatorTime);
  digitalWrite(ELEVATOR_FET, LOW); // Turn servo off.
}

void startElevator(int degrees) {
  digitalWrite(ELEVATOR_FET, HIGH); // Turn servo on.

  int elevatorChange = abs(elevator.read() - degrees);
  elevatorTime = elevatorChange * 170 / 60;
  if (elevatorTime < 40) {
    elevatorTime += 40;
  }
  if (elevatorTime < 60) {
    elevatorTime += 20;
  }

  elevator.write(degrees);
  elevatorStartTime = millis();
  elevatorMoving = true;
}

void updateElevator() {
  if ((millis() - elevatorStartTime > elevatorTime) && elevatorMoving) {
    digitalWrite(ELEVATOR_FET, LOW);
    elevatorMoving = false;
  }
}

// void land(int left, int right) {
//   moveLeftServo(left);
//   moveRightServo(right);
// }

// Experimental stuff below.
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

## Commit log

2024-06-26 Started gpsBreakout
    [gpsBreakout.kicad_pcb, gpsBreakout.kicad_sch]
2024-06-27 Finished board
    [bom.csv, designators.csv, gpsBreakout.kicad_pcb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]
2024-06-28 Folding glider, plus some PCB stuff from later
    [foldingGlider v1.f3d, gpsBreakout.kicad_pcb, gpsBreakout.kicad_sch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]
2024-06-28 Create foldingGlider v2.f3d
    [foldingGlider v2.f3d]
2024-06-30 Starting low power
2024-07-01 Flying wing calculator and more research
2024-07-02 hey I fixed it I think
    [gps.cpp]
2024-07-02 servo algorithim
2024-07-02 Modify imu.ino
2024-07-02 New IMU code
2024-07-09 IMU stuff
    [StratoSoar-MK3.0.kicad_sch, bom.csv, designators.csv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]
2024-07-09 Worked on servo section
    [StratoSoar-MK3.0.kicad_sch]
2024-07-10 More work on the schematic
    [StratoSoar-MK3.0.kicad_sch, gpsBreakout.kicad_sch]
2024-07-10 Finished schematic, started PCB
    [StratoSoar-MK3.0.kicad_pcb, StratoSoar-MK3.0.kicad_sch]
2024-07-10 Basic layout
    [StratoSoar-MK3.0.kicad_pcb, StratoSoar-MK3.0.kicad_sch]
2024-07-11 IMU work
    [StratoSoar-MK3.0.kicad_pcb, StratoSoar-MK3.0.kicad_sch, bom.csv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]
2024-07-11 Added lots of features, made a bunch of bugs!
    [autopilot.ino]
2024-07-11 Code, licensing
    [StratoSoar-MK3.0.kicad_pcb]
2024-07-12 README, IMU
2024-07-13 Finished all connections on PCB
    [StratoSoar-MK3.0.kicad_pcb, StratoSoar-MK3.0.kicad_sch]
2024-07-13 Finished PCB, working on silkscreen
    [StratoSoar-MK3.0.kicad_pcb]
2024-07-13 Mostly silkscreen
    [StratoSoar-MK3.0.kicad_sch]
2024-07-14 RF, silkscreen
    [StratoSoar-MK3.0.kicad_pcb]
2024-07-14 Finished PCB
    [StratoSoar-MK3.0.kicad_pcb, bom.csv, designators.csv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]
2024-07-15 Actually finished board for real?
    [StratoSoar-MK3.0.kicad_pcb, StratoSoar-MK3.0.kicad_sch, gpsBreakout.kicad_sch]
2024-07-15 Actually finished board, did GPS work
    [StratoSoar-MK3.0.kicad_pcb, bom.csv, designators.csv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]
2024-07-16 Work on GPS
    [gpsBreakout.kicad_pcb]
2024-07-16 More gps work
    [bom.csv, designators.csv, gpsBreakout.kicad_pcb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]
2024-07-16 GPS, IMU
    [StratoSoar-MK3.0.kicad_sch, bom.csv, gpsBreakout.kicad_pcb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]
2024-07-17 Cardboard glider
    [cardboardGlider v5.step]
2024-07-17 Almost done!
    [bottomCut.dxf, cardboardGlider v6.step, cut.dxf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]
2024-07-18 Finished script
    [cardboardGlider v8.f3d, cardboardGlider v8.step]
2024-07-18 Finished parametric design?
    [bottomCut.dxf, cardboardGlider v5.step, cardboardGlider v6.step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]
2024-07-20 LoRa PCB
    [StratoSoar-MK3.0.kicad_pcb, loRa.kicad_pcb, loRa.kicad_sch]
2024-07-21 LoRa PCB and case
    [bom.csv, designators.csv, groundStation v2.f3d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]
2024-07-22 PCB case
    [groundStation v4.f3d]
2024-07-29 Best pitch finder.
2024-08-10 Added threading for the uploader
2024-08-13 Different camera
2024-08-23 Almost done with the README
    [StratoSoar Rev2 v36_StratoSoar Rev2 v36_Bumper_1_Body1.stl, StratoSoar Rev2 v36_StratoSoar Rev2 v36_Horizontal mount_1_Horizontal mount.stl, StratoSoar Rev2 v3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]
2024-11-10 I broke it again
    [ahrsThreading.ino, autopilot.ino, servo.cpp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]
2024-11-20 Rewriting ground station code
2024-12-01 it actually fucking works
    [KC1SFR.csv, stations.csv]

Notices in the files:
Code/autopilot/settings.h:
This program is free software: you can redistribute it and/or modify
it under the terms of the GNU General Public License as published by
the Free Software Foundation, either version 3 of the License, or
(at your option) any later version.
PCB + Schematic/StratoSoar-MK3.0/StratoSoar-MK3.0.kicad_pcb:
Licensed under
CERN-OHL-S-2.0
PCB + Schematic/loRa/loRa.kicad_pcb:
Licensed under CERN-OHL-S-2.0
